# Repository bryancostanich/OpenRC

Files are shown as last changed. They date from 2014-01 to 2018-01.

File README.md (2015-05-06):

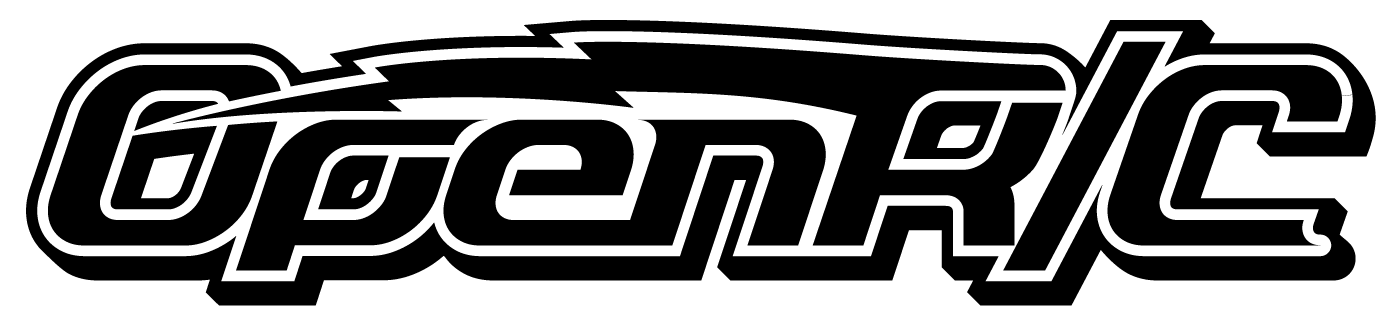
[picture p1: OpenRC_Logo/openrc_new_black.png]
OpenRC Logo


Repo for the OpenRC Printable Radio Controlled Vehicles Project. Contains printable parts, instructions, and parts sourcing info. Based on the [Google Group here](https://plus.google.com/communities/112745535856143176146)

# [General RC Information](RCInfo.md)
Battery info, radio info, etc.

# Projects

## [Truggy](Truggy)

An awesome 4WD 1:10 Scale 3D printable truggy! This pic says all about this sexy beast:

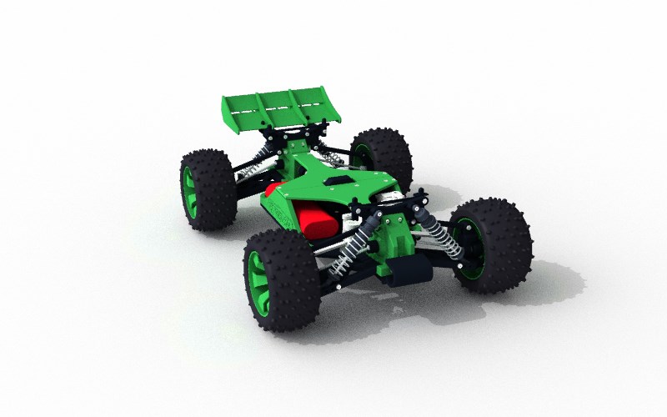
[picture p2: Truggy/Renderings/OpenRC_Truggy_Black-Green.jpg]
Truggy Pic


## [Touring Car](https://github.com/bryancostanich/OpenRC/tree/master/Touring_Car)

4WD 1:10 scale 3D Printable touring car. Also designed by Daniel, the Touring Car was his first attempt at designing an RC Car.

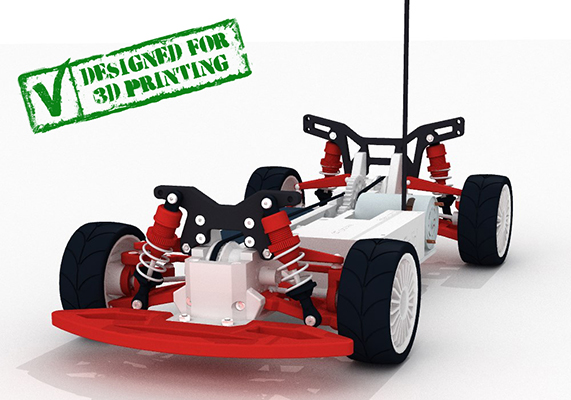
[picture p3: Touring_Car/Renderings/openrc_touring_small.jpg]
Touring Car Pic


## [Ducted Fan Design Library](DuctedFanDesignLibrary)

An electric ducted fan design library written in Python using the Blender API. Currently, the software is in script form, but an add-on of sorts is being created.

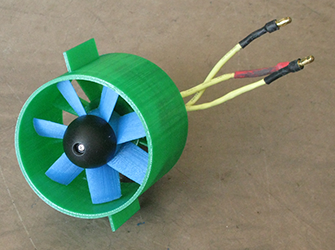
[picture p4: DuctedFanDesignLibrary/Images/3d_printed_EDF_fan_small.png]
Fan


## Authors
 * Truggy - Daniel Norée
 * Ducted Fan Design Library - André Roy

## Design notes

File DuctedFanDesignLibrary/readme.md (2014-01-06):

# Ducted Fan Design Library
An electric ducted fan design library written in Python using the Blender API. Currently, the software is in script form, but an add-on of sorts is being created.

Fan

## Instructions

 * Load blender
 * Split the default 3d window vertically and open the text editor in the new left window.
 * In the text editor open **EDFLibrary.py**, **DLUtils.py**, **TurboMachLib.py** and **GUI.py**
 * Run the **GUI.py** script
 * New tools will appear in the object tools pane of the 3D window on the right.

## License
[GNU Affero GPL V3.0](http://www.gnu.org/licenses/agpl-3.0.html)

Copyright DesignLibre 2013.

Author: André Roy

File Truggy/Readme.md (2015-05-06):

# OpenRC Truggy

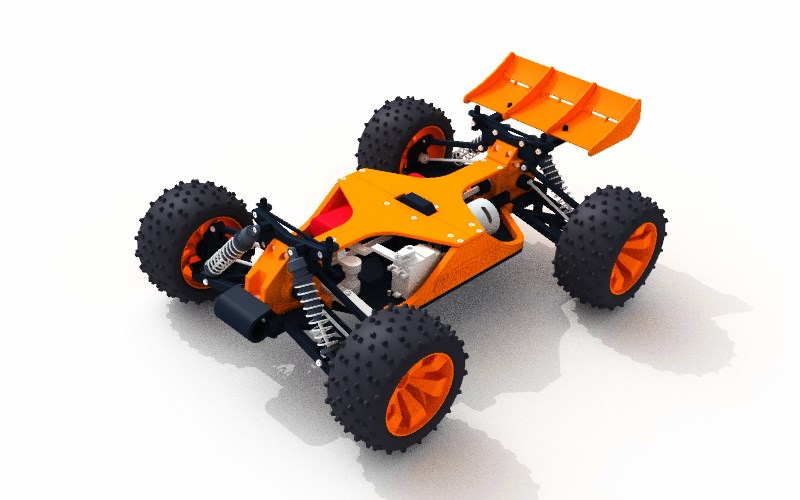
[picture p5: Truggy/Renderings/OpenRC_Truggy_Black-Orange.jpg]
Truggy


## Introduction
 * **video** - [Here](http://www.youtube.com/watch?v=dElz53EsmtM)
 
## License
Truggy has been released under the [Creative Commons 3.0 License](http://creativecommons.org/licenses/by/3.0/), Copyright Daniel Norée
 
## File Organization
I've taken a whack at organizing the files, but please let me know if you want to be added to the repo and organize even more/better.
 
## Bill of Materials and Sourcing Info
 * [here](https://github.com/bryancostanich/OpenRC/blob/master/Truggy/BOM.md)

## Documentation
 * [here](Documentation)

## Specs

### Dimensions
 * **Class** - 1/10 electric 4WD Truggy
 * **Width** - 312 mm
 * **Length** - N/A mm
 * **Wheelbase** - 280 mm
 * **Ready-to-run weight** - 2100 g Chassis

### Chassis Plate
 * **Chassis Plate** - 2Pcs 3D Printed ABS (1 pc version available)
 * **Top Deck** - 2Pcs 3D Printed ABS

### Suspension
 * **Shocks** - 3D Printed Nylon OpenRC Shocks

### Drivetrain
* **Type** - Full-time shaft-drive 4WD
* **Primary** - Pinion / spur
* **Drive shafts** - Reely CVD-cardan shaft (V23581L)
* **Central shafts** - 3DPrintedABSDirectConnectionShafts
* **Differentials** - 3D Printed ABS + Nylon combo
* **Bearings** - Rubber-sealed high-speed bearings

### Gearing
 * **Primary ratio** - ￼1:2.5
 * **Differential pinion** - 16T front / rear
 * **Differential crown gear** - 40T front / rear
 * **Spur gear** - 65T
 * **Motor pinion** - 20T
 
### Geometry
 * **Camber** - Adjustable front & rear, 3D Print replacement parts
 * **Caster** - 6.5º Static
 * **Toe-in** - Adjustable front , 3D Print replacement parts
 * **Steering** - Centrally-positioned dual steering system W/O servo saver
 
### Body, Tires, Wheels & Misc
 * **Body** - HPI Firestorm
 * **Tires** - Losi 320S Zombie Max
 * **Wheels** - 3D Printed ABS OpenRC Truggy Rims
 
### Electronics 
 * **Radio system** - Hobby King GT-2 2.4Ghz 2Ch Tx & Rx
 * **Motor** - Turnigy Trackstar 3650 16T (4000Kv) Brushless Motor
 * **Esc** - Turnigy Trackstar 80A Sensorless Brushless ESC
 * **Battery** - Turnigy 4000mAh 2S 40C Lipo Pack

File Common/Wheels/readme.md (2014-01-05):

# Wheels
 * Beadlock Rim - [outcast RC @ thingiverse](http://www.thingiverse.com/thing:47271)
 * OZ Rally WRC (M-03_OZ-WRC) - [breckandawson @ github](https://github.com/brackendawson/M-03_wheels)
 * my_rim_2.skp - [Cain666 @ Thingiverse.com](http://www.thingiverse.com/thing:144591)]
 * RC Crawler 4x4 - [diegudio @ thingiverse](http://www.thingiverse.com/thing:176945)

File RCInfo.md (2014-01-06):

# RC Vehicle Information
## Battery Choice
 * [LiPo vs. LiFe vs. LiIon Comparison](http://www.brighthubengineering.com/power-generation-distribution/123906-comparison-of-lithium-ion-to-lithium-iron-battery/)

battery comparison

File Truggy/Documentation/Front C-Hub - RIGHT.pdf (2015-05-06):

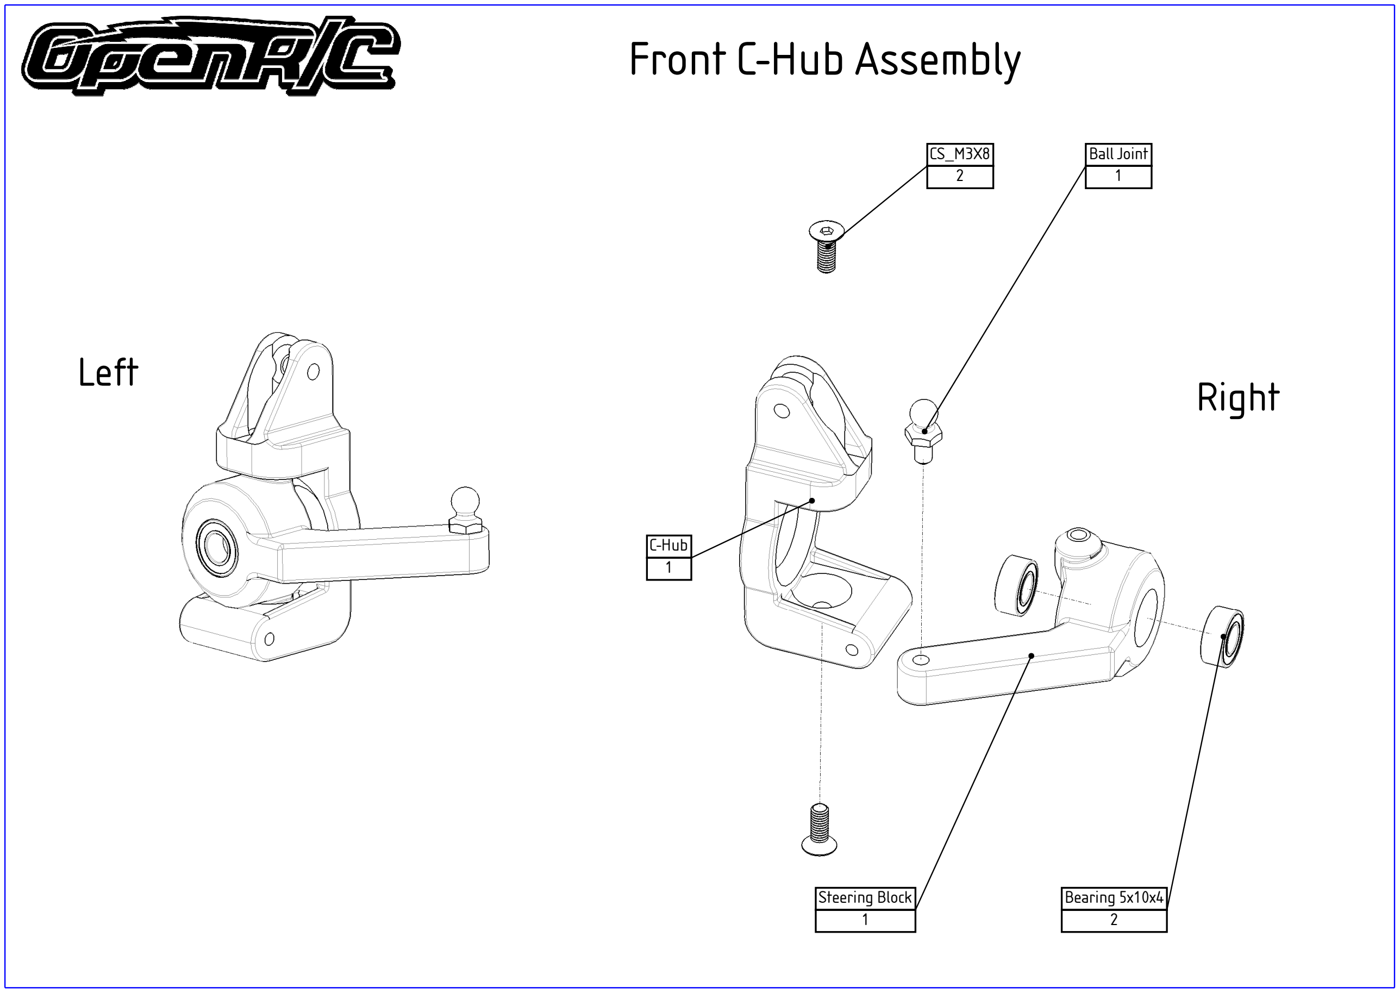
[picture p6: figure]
Front C-Hub Assembly; Left; Right; Bearing 5x10x4 2; C-Hub 1; Steering Block 1; Ball Joint 1

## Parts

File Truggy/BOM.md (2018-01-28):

# Truggy Bill of Materials

## Hardware

### Screws
 * (54) Hexagon Socket Countersunk Head Screw ISO 10642 - M3 × 8 
 * (8) Hexagon Socket Countersunk Head Screw ISO 10642 - M3 × 12
 * (4) Hexagon Socket Countersunk Head Screw ISO 10642 - M3 × 16
 * (10) Hexagon Socket Pan Head Cap Screw ISO 7380 - M3 × 8
 * (10) Hexagon Socket Pan Head Cap Screw ISO 7380 - M3 × 10
 * (12) Hexagon Socket Pan Head Cap Screw ISO 7380 - M3 × 12
 * (4) Hexagon Socket Pan Head Cap Screw ISO 7380 - M3 × 14
 * (4) Hexagon Socket Pan Head Cap Screw ISO 7380 - M3 × 16
 
#### Screw Sources

 * [M3 Hexagon Socket Countersunk Head Screw, various materials and lengths @ Amazon Supply](http://www.amazonsupply.com/s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)
 * [ISO 7380 M3 Button (Pan) Head Cap Screws, various materials and lengths @ Amazon Supply](http://www.amazonsupply.com/s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)
 
###  Nuts

 * (26) M3 Hexagon Nut ISO 4032 - [Amazon Source](http://www.amazon.com/dp/B000FN0CP0/ref=biss_dp_t_asn)
 
### Bearings
 * (10) 10x15x4 - [Amazon Supply Source](http://www.amazonsupply.com/s/ref=sp_search?guess=true&Action=submit&keywords=10x15x4+bearing)
 * (8) 5x10x4 - [Amazon Supply Source](http://www.amazonsupply.com/s/ref=sp_search?guess=true&Action=submit&keywords=5x10x4+bearing)
 * (4) 6x12x4 - [Amazon Supply Source](http://www.amazonsupply.com/s/ref=sp_search?guess=true&Action=submit&keywords=6x12x4+bearing)

### Rods
 * (4) Ø2.0 x 32mm
 * (3) Ø3.0 x 18mm
 * (4) Ø3.0 x 56mm
 * Optional: Ø2.0 x 10mm for internal driveshafts
 
### Drivetrain
 * (4) Outer Driveshafts - CVD 1:10 118MM (See sources)
 
### Wheels
 * (4) Rims - Printed OpenRC
 * (4) Tires - Losi 320S Zombie Max Tire with Foam LOSB7213
 
### Suspension
 * (4) 100mm Standard RC Car Shocks
 	* [Blue Aluminum @ HobbyKing.com](http://www.hobbyking.com/hobbyking/store/__22499___1_10_Model_Car_100mm_Adjustable_Aluminum_Shock_Absorber_2pc_Blue_.html)
 	* [Purple Aluminum @ HobbyKing.com](http://www.hobbyking.com/hobbyking/store/__26276__1_10_Car_100mm_Aluminum_Shock_Absorber_Purple_2pcs_bag_.html)
 	* [Silver Aluminum @ HobbyKing](http://www.hobbyking.com/hobbyking/store/__22500__1_10_Model_Car_100mm_Adjustable_Aluminum_Shock_Absorber_2pc_.html)
 	* [Gun Metal Aluminum with Three Pairs of Various Strength Spings @ TowerHobby.com](http://www3.towerhobbies.com/cgi-bin/wti0001p?&I=LXDCTM&P=7)
 
###  Body
 * Body - HPI Firestorm DSX-1 Lexan Truck Body HPI7123
 
## RC Components

### Motor + Electronic Speed Controller (ESC)
Standard 1:10  motor rated for 4WD.

 * [Castle Creations SV3 Sidewinder 6900kV @ TowerHobbies.com](http://www3.towerhobbies.com/cgi-bin/wti0001p?&I=LXDAVR&P=7)
 * [Castle Creations SV3 Sidewidner 7700kV @ TowerHobbies.com](http://www3.towerhobbies.com/cgi-bin/wti0001p?&I=LXDAVS&P=7)
 * [OUT OF STOCK - Turnigy TrackStar Waterproof 1/10 Brushless Power System 4000KV/80A (Motor+ESC Combo)](http://www.hobbyking.com/hobbyking/store/uh_viewItem.asp?idProduct=25138 @ HobbyKing.com)

### Battery

 * [Turnigy 4000mAh 2S 40C Lipo Pack @ HobbyKing.com](http://www.hobbyking.com/hobbyking/store/RC_PRODUCT_SEARCH.asp?strSearch=Turnigy+4000mAh+2S+40C)

### Battery Charger

 * [Ace T6DC Digital Multi Charger @ TowerHobbies.com](http://www3.towerhobbies.com/cgi-bin/wti0001p?&I=LXBFDR&P=7)

### Servo

 * [BMS-620MG High Torque Servo (Metal Gear) 9.1kg / .15sec / 50g](http://www.hobbyking.com/hobbyking/store/RC_PRODUCT_SEARCH.asp?strSearch=BMS-620MG)

### Radio

Standard 2 Channel Transmitter and Receiver (Radio System)

 * [Hobby King GT-2 2.4Ghz 2Ch Radio System](http://www.hobbyking.com/hobbyking/store/RC_PRODUCT_SEARCH.asp?strSearch=Hobby+King+GT-2+2.4Ghz+2Ch)
 * [Tower Hobbies 224 2-channel 2.4ghz Radio System](http://www3.towerhobbies.com/cgi-bin/wti0001p?&I=LXWPW0&P=7)
 * [Tactic TTX240 2-Channel SLT 2.4ghz Radio System @ TowerHobbies.com](http://www3.towerhobbies.com/cgi-bin/wti0001p?&I=LXWRP3&P=7)
 * [HPI Racing TF-40 2.4ghz Radio System @ TowerHobbies.com](http://www3.towerhobbies.com/cgi-bin/wti0001p?&I=LXCEHR&P=7)
 * [Axial AX-3 2-Channel 2.4ghz Radio System @ TowerHobbies.com](http://www3.towerhobbies.com/cgi-bin/wti0001p?&I=LXBMCM&P=7)
 
### CVD Shafts
 * [Conrad](http://www.conrad.com/ce/en/product/231121/)

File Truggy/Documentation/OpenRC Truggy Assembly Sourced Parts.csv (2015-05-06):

Name |  |  |  |  |  | Quantity
Adhesive tape (For battery holder) | 1
Ball Joint |  |  |  |  | 5
Bearing 5x10x4 |  |  |  | 8
Bearing 6x12x4 |  |  |  | 4
Bearing 10x15x4 |  |  |  | 10
CS_M3X5,5 (Cut from a longer screw) | 1
CS_M3X8 |  |  |  |  | 54
CS_M3X10 |  |  |  |  | 6
CS_M3x14 |  |  |  |  | 4
CS_M3x16 |  |  |  |  | 6
HSC_M3X8 |  |  |  |  | 3
HSC_M3X10 |  |  |  |  | 14
HSC_M3X14 |  |  |  |  | 8
HSC_M3X16 |  |  |  |  | 14
NUT_M3 |  |  |  |  | 26
NUT_M4 |  |  |  |  | 4
Pin 2x10 |  |  |  |  | 8
Pin 2x32 |  |  |  |  | 4
Pin 3x18 |  |  |  |  | 3
Pin 3x56 |  |  |  |  | 4
CVD Driveshaft 118mm |  |  | 4
Velcro (For battery holder) |  | 1

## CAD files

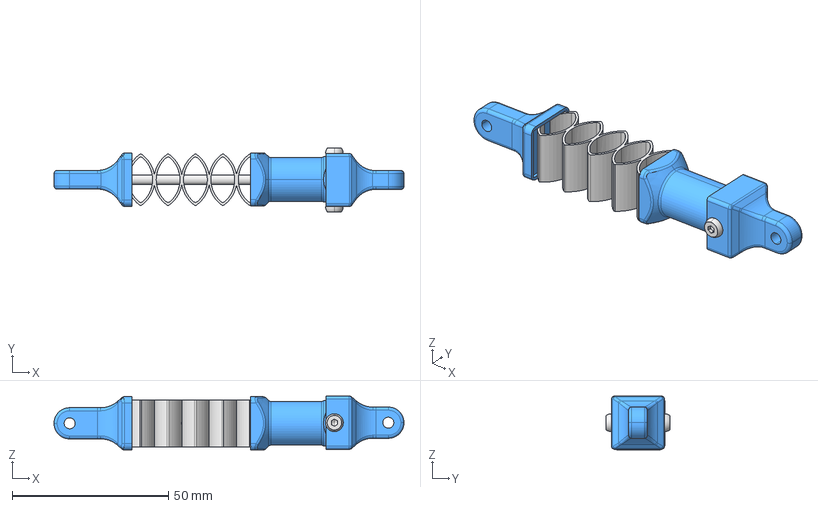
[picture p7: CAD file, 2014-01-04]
Truggy/STLs of Components for Printing/Suspension/Experimental Shocks/STP/Open RC Experimental Shock Assembly.stp
111.9 x 20.3 x 17.2 mm
Spring
Bottom
Lid
Hexagon Socket Head Cap Screw ISO 4762 - M3 _ 30
Hexagon Socket Pan Head Cap Screw ISO 7380 - M3 × 6 x 2

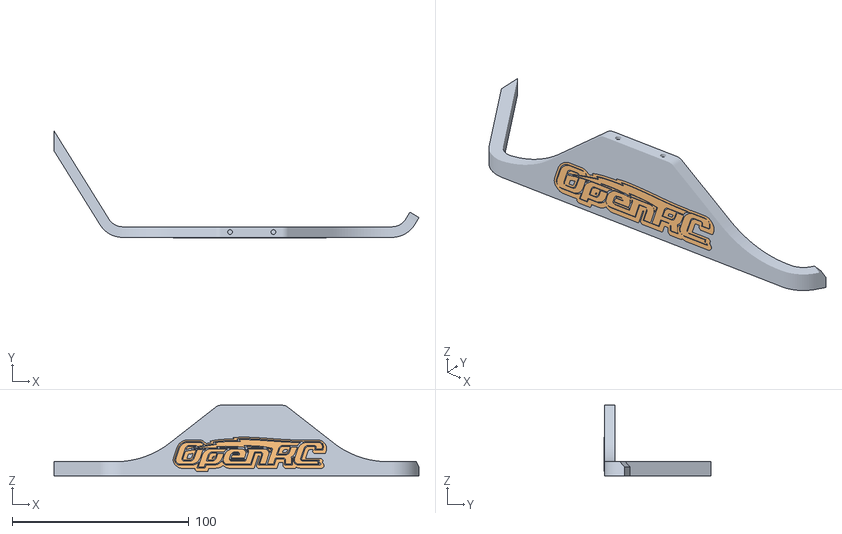
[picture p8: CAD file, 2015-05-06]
Truggy/STLs of Components for Printing/Chassis/Right Shield Assy w Logo.stl
206.8 x 60.8 x 40.0

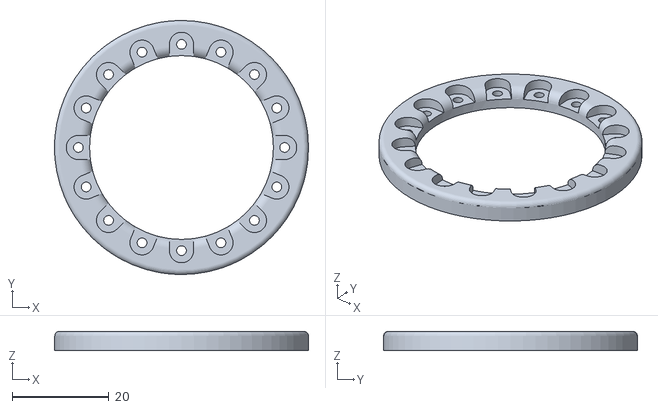
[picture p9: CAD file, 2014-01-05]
Common/Wheels/Beadlock Rim/bead_thick.stl
52.5 x 52.5 x 4.00

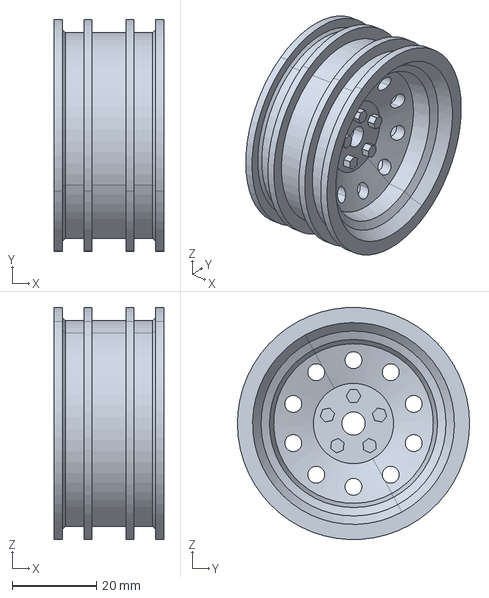
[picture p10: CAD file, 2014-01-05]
Common/Wheels/RC Crawler 4x4 Rim/llanta_v1.1.stp
26.0 x 55.0 x 55.0 mm

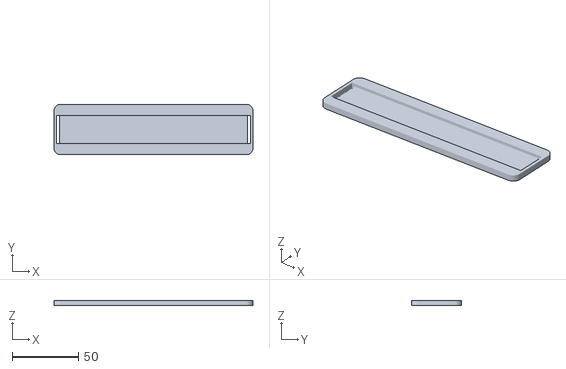
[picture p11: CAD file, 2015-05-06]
Truggy/STLs of Components for Printing/Battery Holder/Battery Holder.stl
150.0 x 38.0 x 4.00

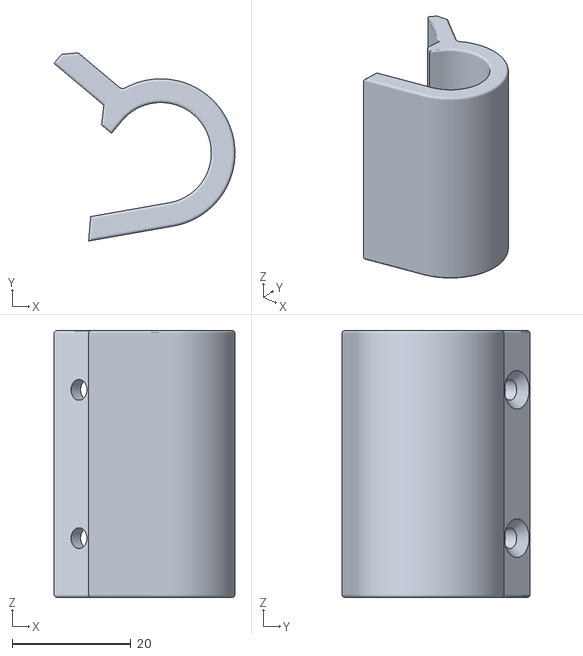
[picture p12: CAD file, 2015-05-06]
Truggy/STLs of Components for Printing/Bumper/Bumper.stl
30.5 x 31.7 x 45.0

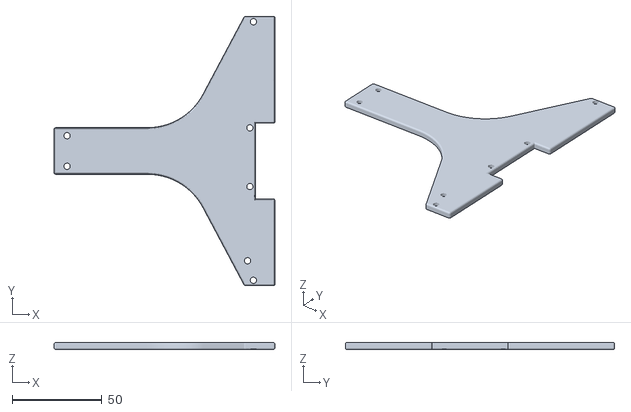
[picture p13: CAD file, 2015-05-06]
Truggy/STLs of Components for Printing/Chassis/Top Deck Rear.stl
123.1 x 150.0 x 4.00

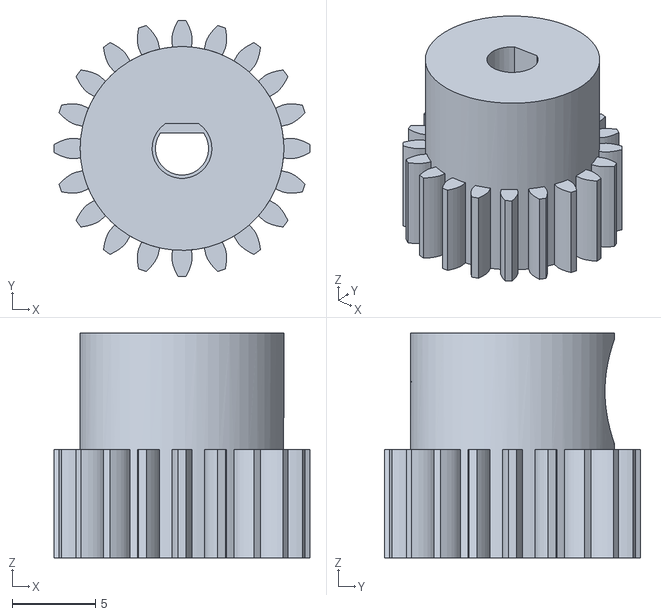
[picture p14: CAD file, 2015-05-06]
Truggy/STLs of Components for Printing/Drive Train/Spur Gear 20T.stl
15.4 x 15.4 x 13.5

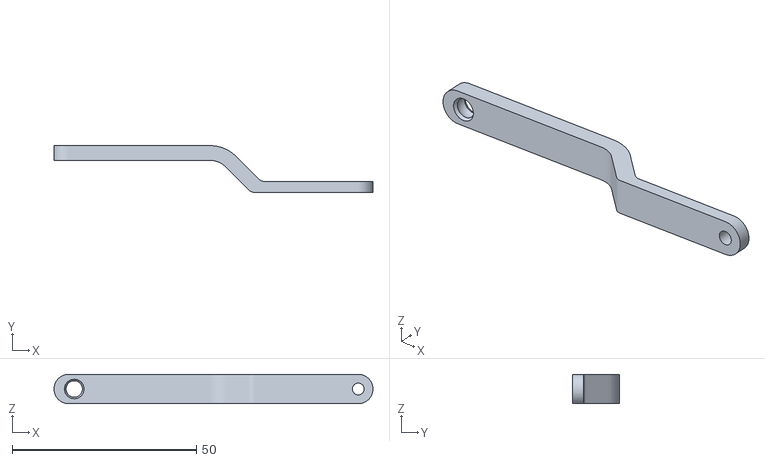
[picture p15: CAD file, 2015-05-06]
Truggy/STLs of Components for Printing/Electronics Holders/Servo Arm.stl
86.6 x 12.7 x 8.00

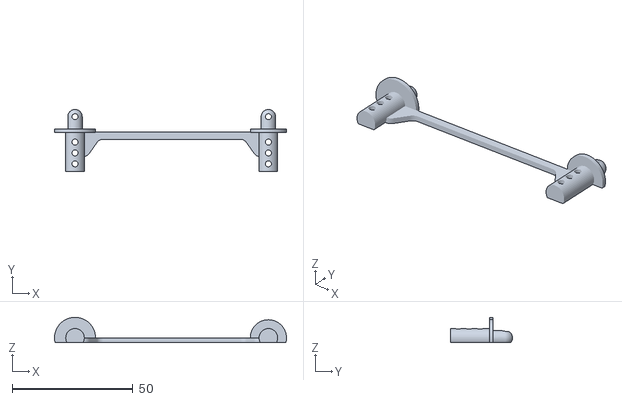
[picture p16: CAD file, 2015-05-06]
Truggy/STLs of Components for Printing/Misc/Simple Body Holder.stl
96.0 x 25.7 x 10.5

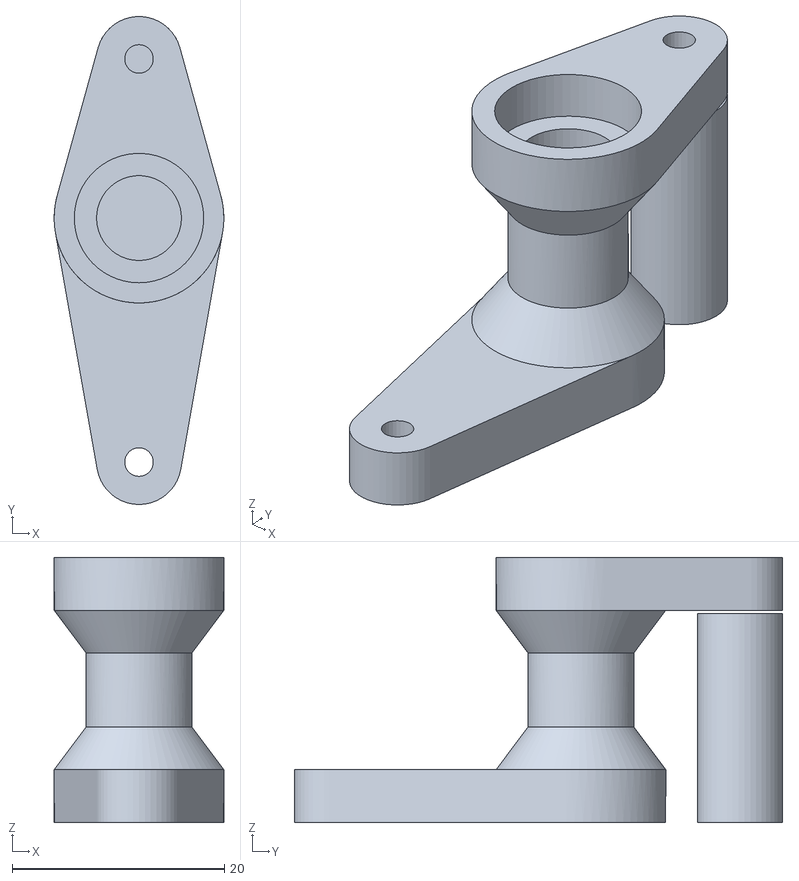
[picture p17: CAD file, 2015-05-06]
Truggy/STLs of Components for Printing/Steering/Steering Part 2.stl
16.0 x 46.0 x 25.0

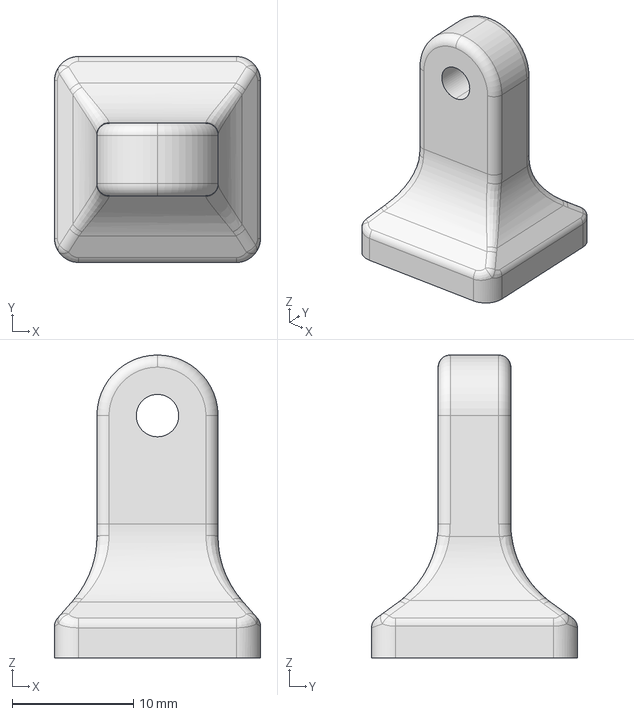
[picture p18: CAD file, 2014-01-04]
Truggy/STLs of Components for Printing/Suspension/Experimental Shocks/STP/Bottom.stp
17.0 x 17.0 x 25.0 mm

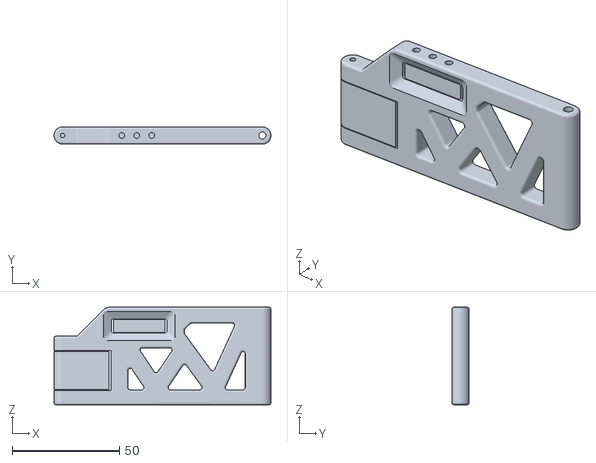
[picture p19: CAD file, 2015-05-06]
Truggy/STLs of Components for Printing/Suspension/Wishbone Front For 118mm Driveshaft.stl
101.0 x 8.00 x 45.5

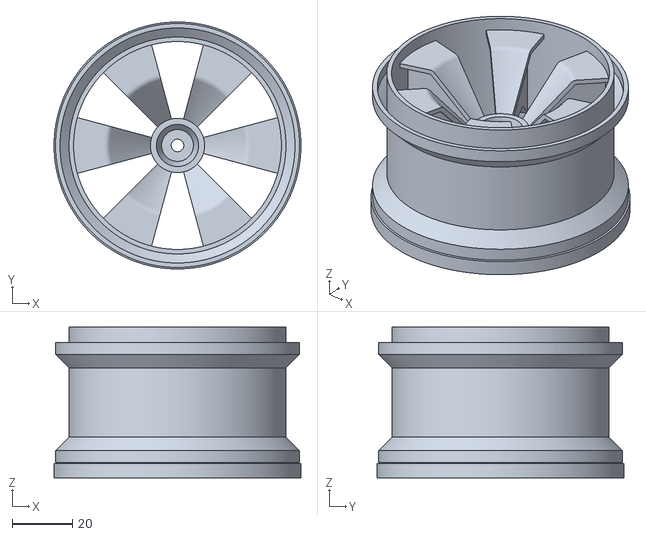
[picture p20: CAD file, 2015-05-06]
Truggy/STLs of Components for Printing/Wheels + Tires/OpenRC Truggy Rim.stl
82.0 x 82.0 x 50.0

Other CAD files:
Truggy/STLs of Components for Printing/Chassis/Left Shield Assy w Logo.stl
Common/Wheels/OZ Rally WRC/M-03_OZ-WRC.stl
OpenRC_Logo/openrc_new_dxf.dxf
Truggy/Tools/STP/Diff Tool.stp
Common/Wheels/Beadlock Rim/bead-scalllop.stl
Common/Wheels/Beadlock Rim/bead-toothed.stl
Common/Wheels/Beadlock Rim/bead-wide.stl
Common/Wheels/Beadlock Rim/bead.stl
Common/Wheels/Beadlock Rim/rim-5spoke.stl
Common/Wheels/Beadlock Rim/rim-8spoke.stl
Common/Wheels/Beadlock Rim/rim-largeholes.stl
Common/Wheels/Beadlock Rim/rim-slot.stl
Common/Wheels/Beadlock Rim/rim-smallholes.stl
Common/Wheels/Beadlock Rim/ring.stl
Common/Wheels/RC Crawler 4x4 Rim/llanta_v1.1.CATPart
Common/Wheels/RC Crawler 4x4 Rim/llanta_v1.1.igs
Common/Wheels/RC Crawler 4x4 Rim/llanta_v1.1.stl
Common/Wheels/my_rim_2.skp
Truggy/STLs of Components for Printing/Chassis/Chassie Plate Front.stl
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

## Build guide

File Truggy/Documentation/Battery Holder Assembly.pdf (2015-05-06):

# Battery Holder Assembly

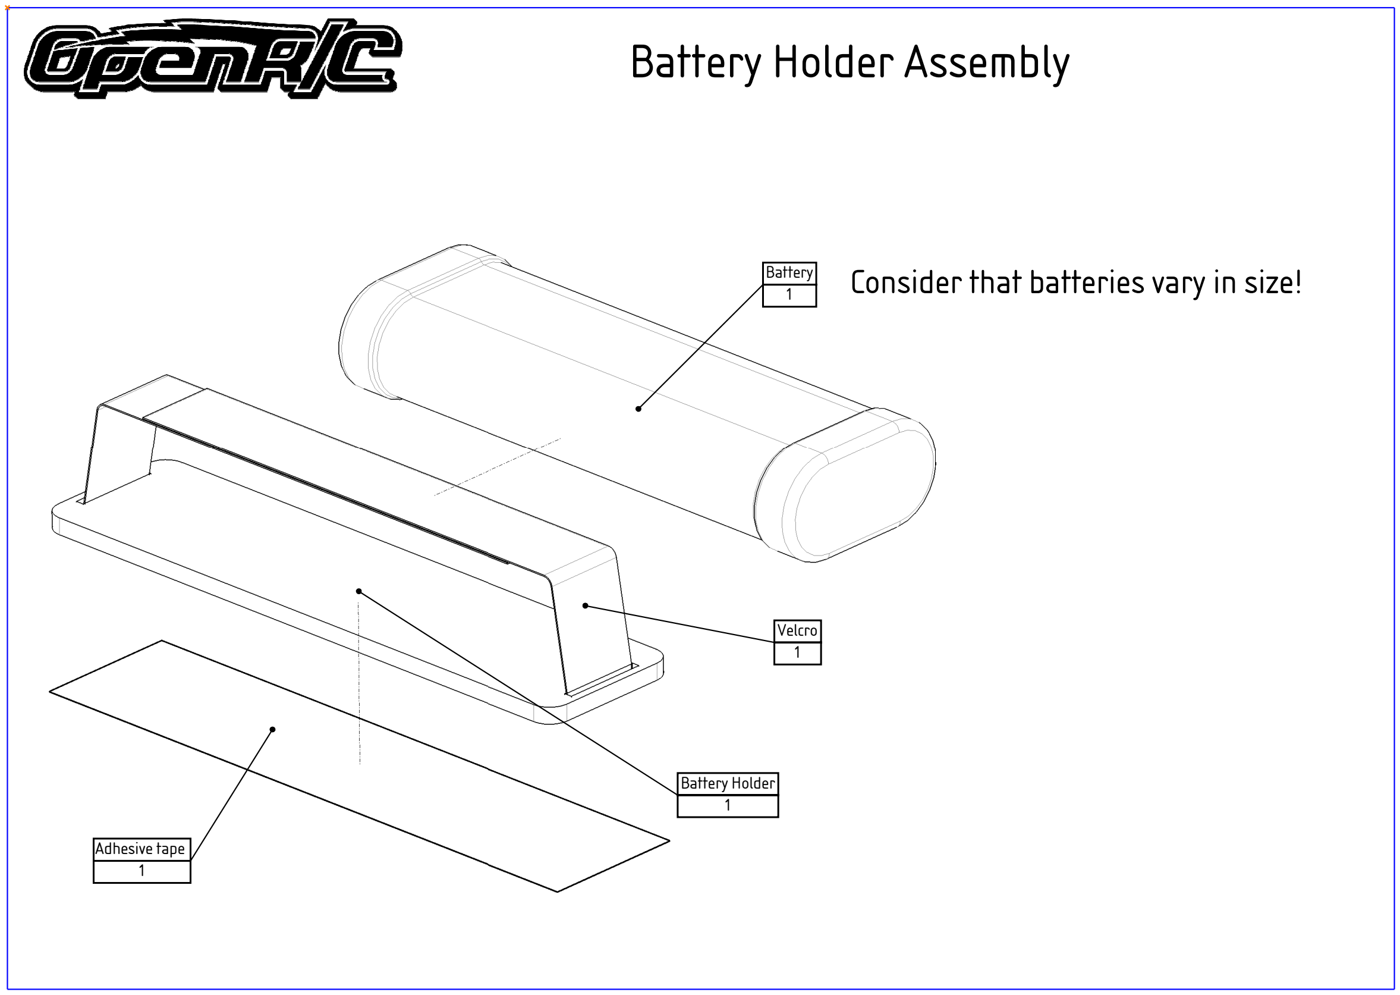
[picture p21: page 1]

Velcro
1

Battery
1

Adhesive tape
1

Battery Holder
1

# Consider that batteries vary in size!

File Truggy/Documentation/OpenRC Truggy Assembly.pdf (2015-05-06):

OpenRC Truggy Assembly

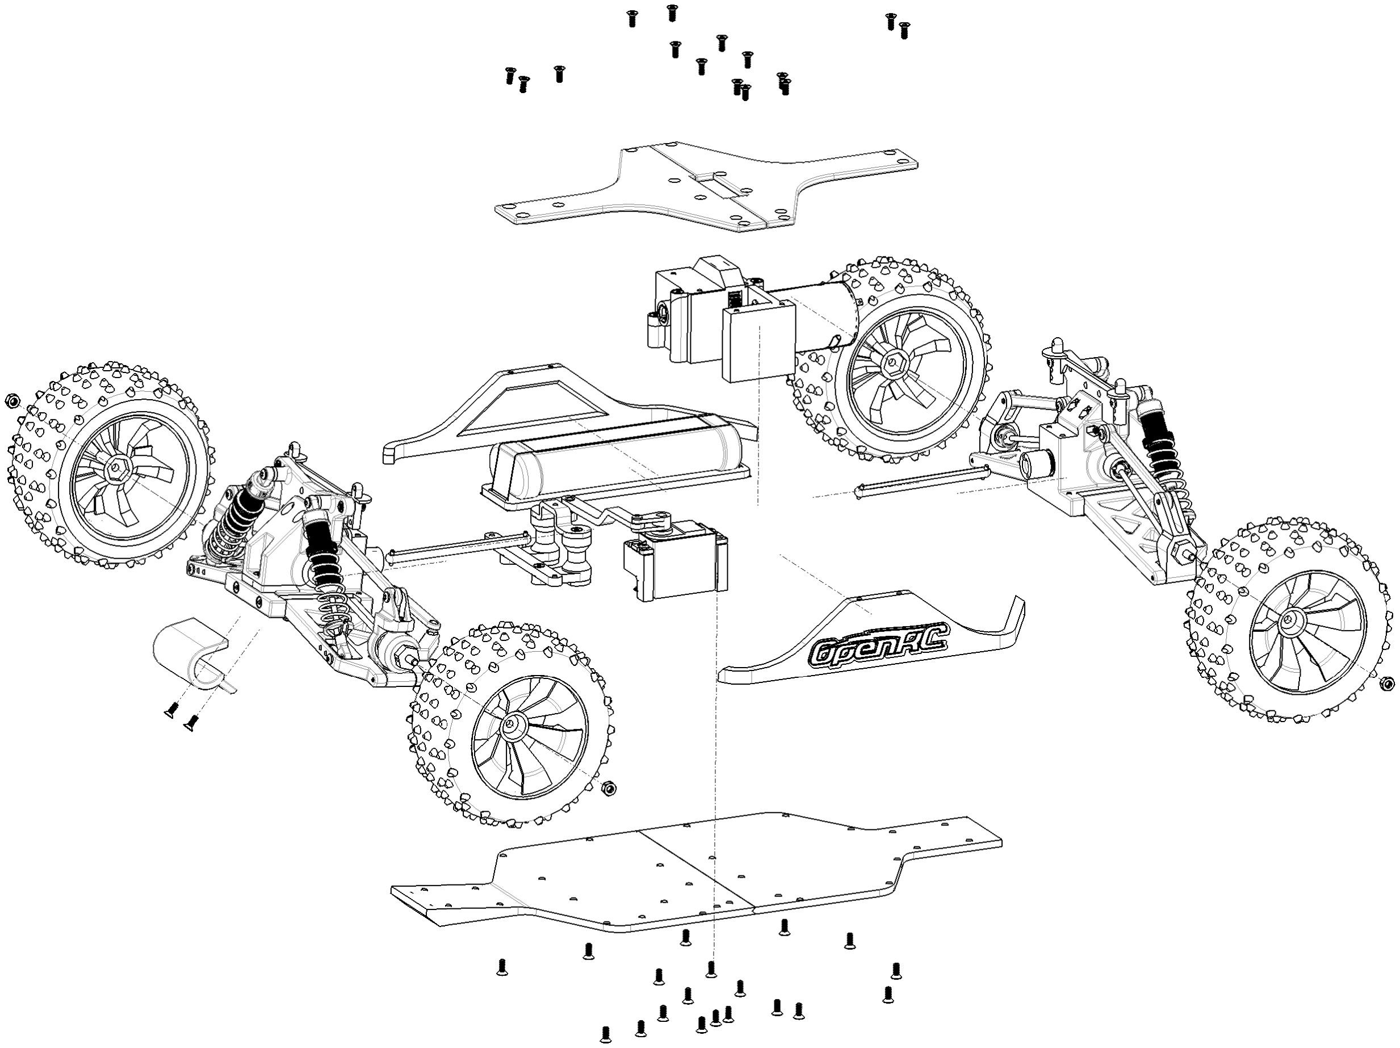
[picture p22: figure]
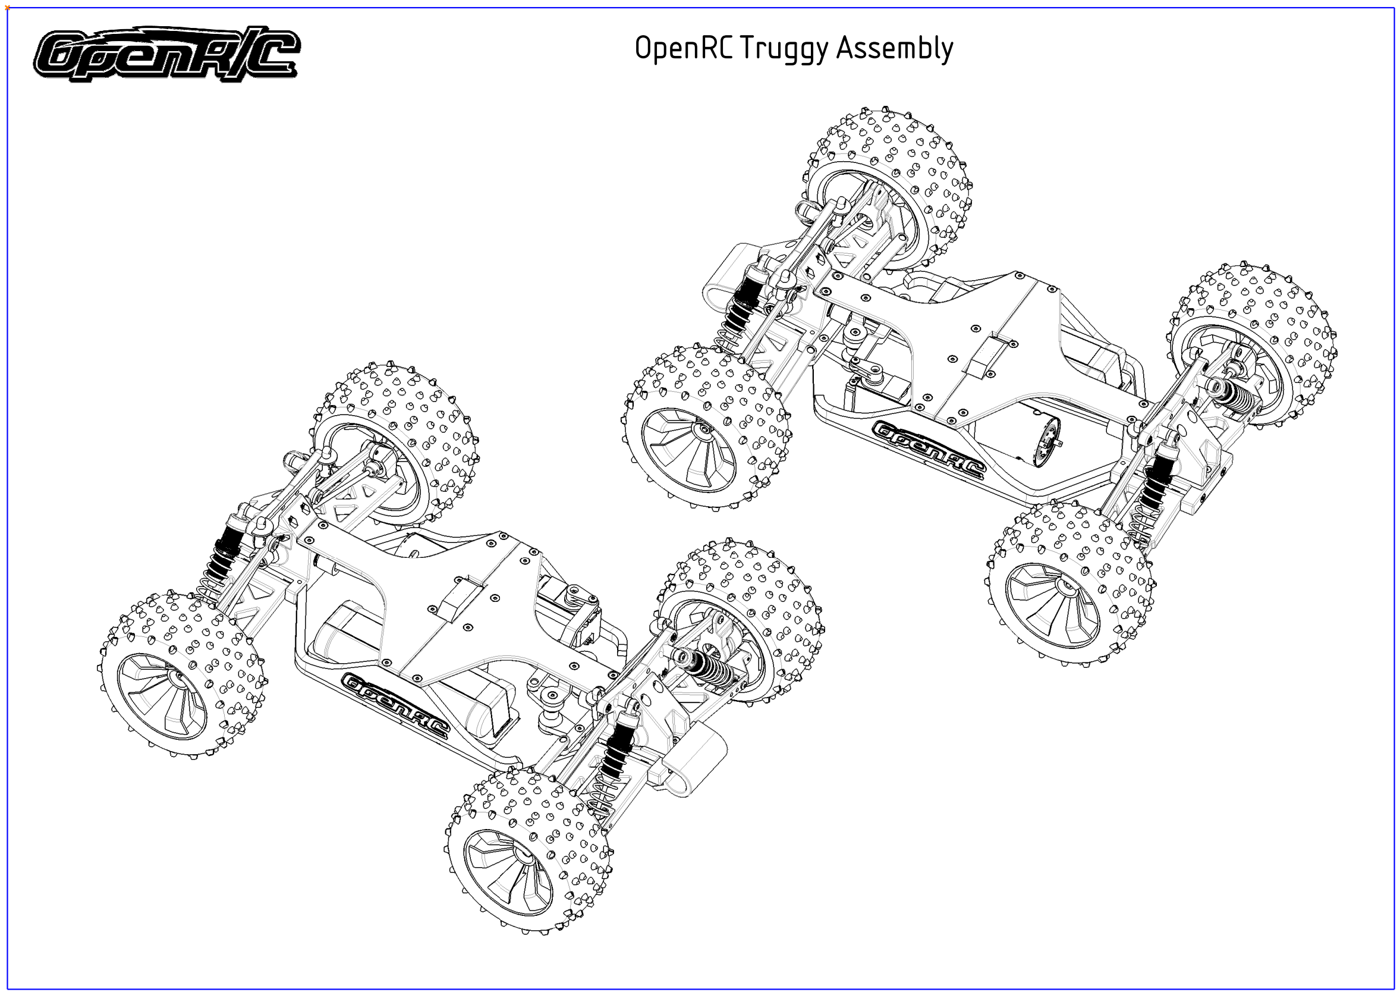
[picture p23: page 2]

OpenRC Truggy Assembly

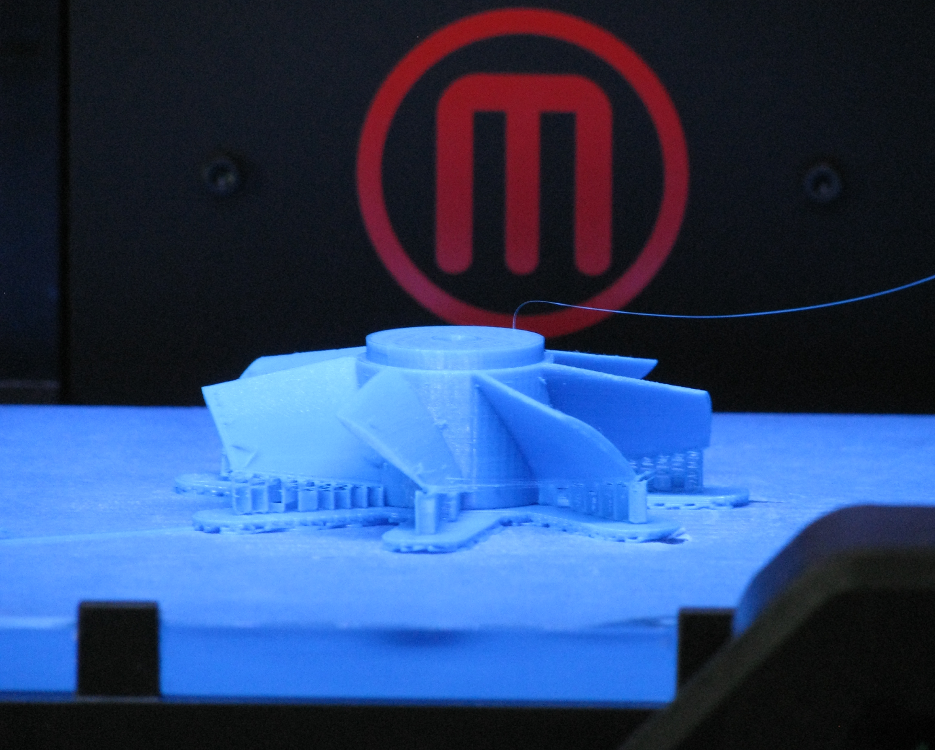
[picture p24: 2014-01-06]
DuctedFanDesignLibrary/Images/blue_3d_printed_EDF_rotor.png

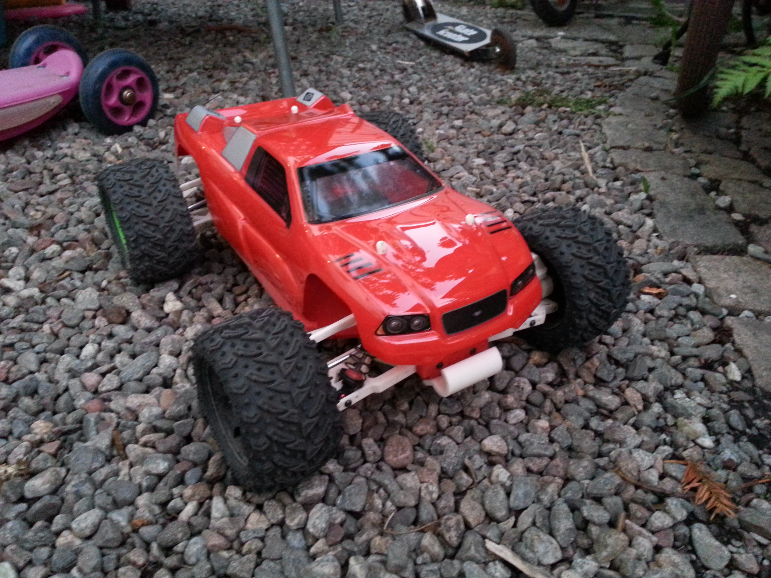
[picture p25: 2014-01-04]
Truggy/Build Pictures/IMG_20130603_220738.jpg

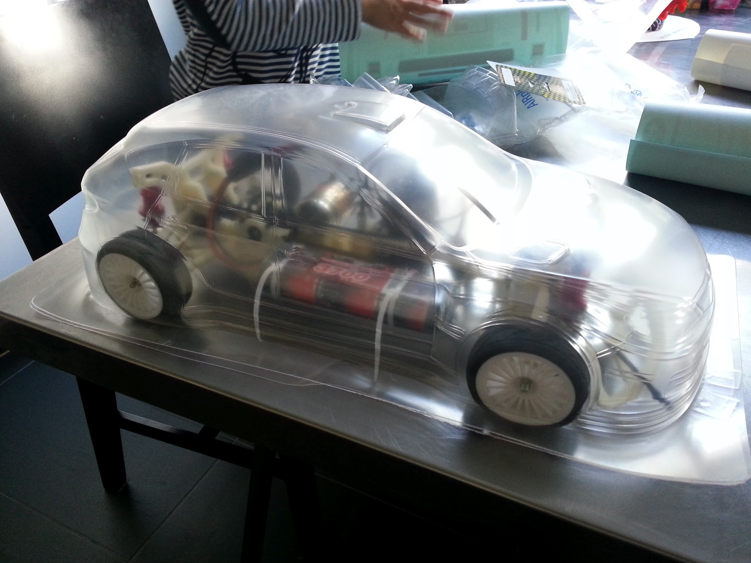
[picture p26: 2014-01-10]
Touring_Car/Build Pictures/20120813_150916.jpg

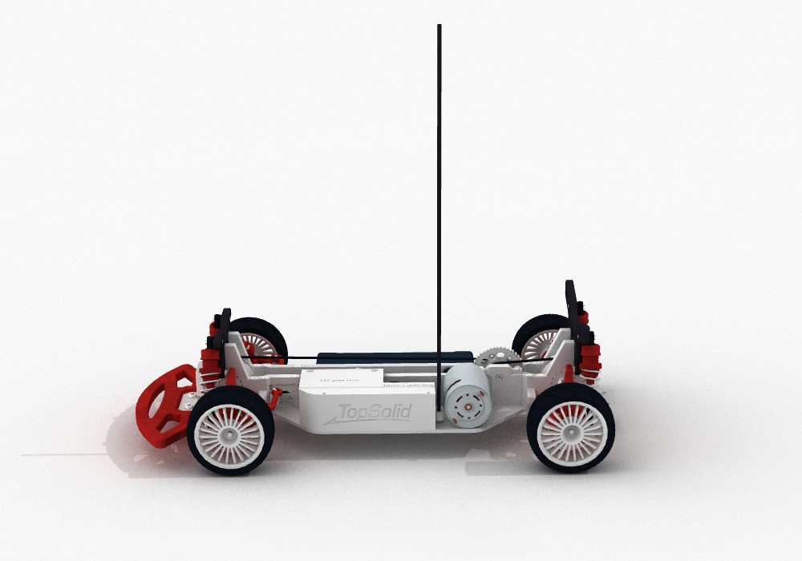
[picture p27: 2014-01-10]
Touring_Car/Renderings/Car Assembly side.jpg

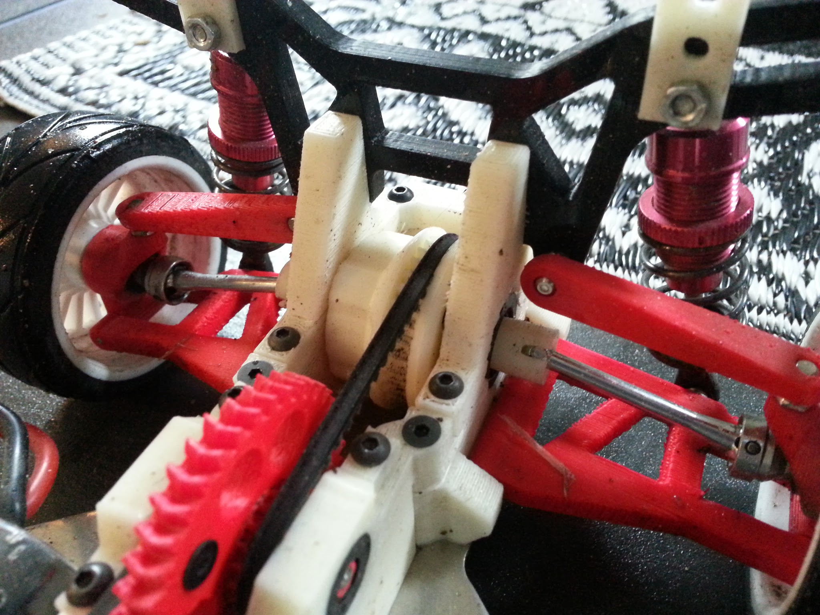
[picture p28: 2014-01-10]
Touring_Car/Build Pictures/IMG_20121110_103743.jpg

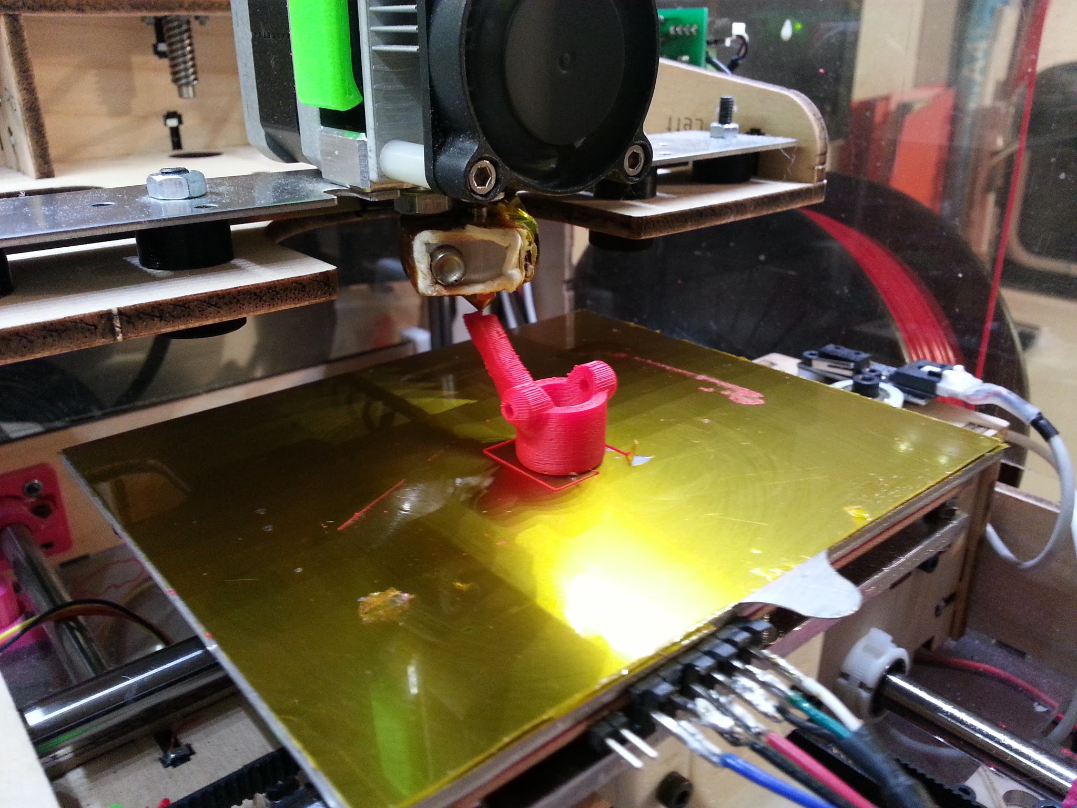
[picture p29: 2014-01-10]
Touring_Car/Build Pictures/20120925_214647.jpg

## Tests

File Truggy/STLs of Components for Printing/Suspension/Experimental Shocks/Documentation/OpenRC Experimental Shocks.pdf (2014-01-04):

### OpenRC Experimental Shocks

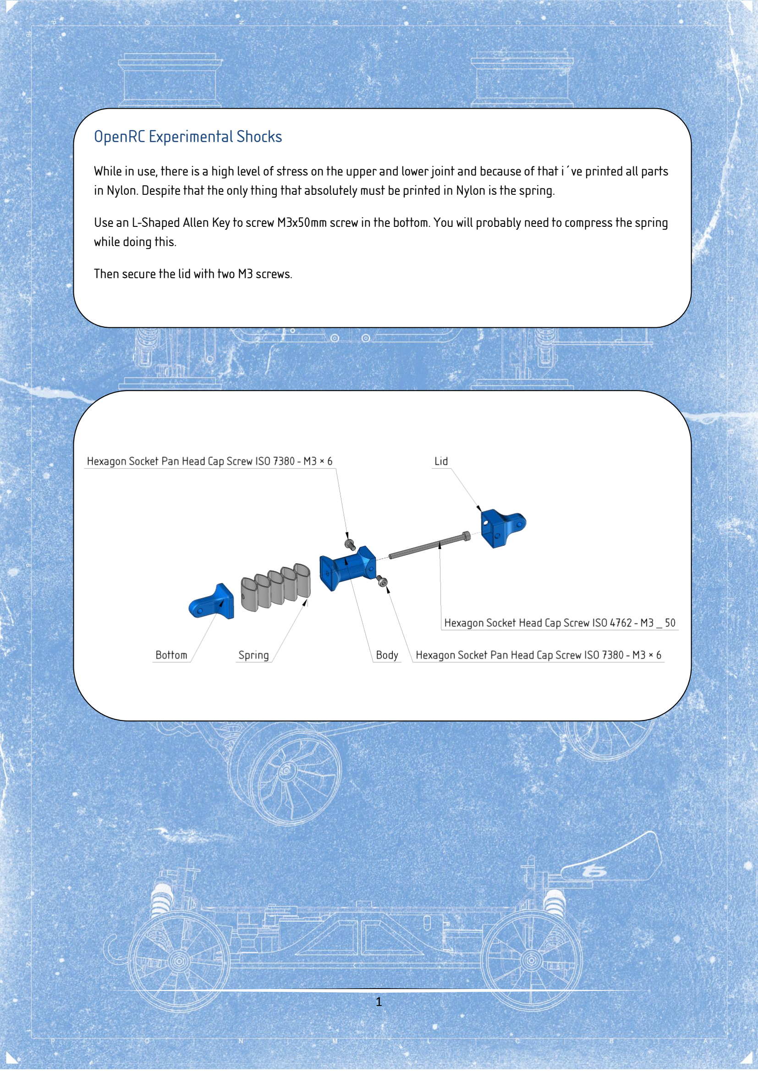
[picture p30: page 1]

1

While in use, there is a high level of stress on the upper and lower joint and because of that i´ve printed all parts in Nylon. Despite that the only thing that absolutely must be printed in Nylon is the spring.

Use an L-Shaped Allen Key to screw M3x50mm screw in the bottom. You will probably need to compress the spring while doing this.

Then secure the lid with two M3 screws.

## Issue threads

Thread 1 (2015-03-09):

Ball connectors

cheeseoverdose, 2015-03-09:
this doesn't include the ball connectors for this build

eLEcTRiCZiTy, 2019-05-03:
Please, include Ball Joints, etc. into BOM.

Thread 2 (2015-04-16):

Bearing 3x10x4 should be 5x10x4?

jb137, 2015-04-16:
Bearings arrived today. But the 3x10x4 does not fit in the CVDs from Conrad. I just discovered the openrcproject BOM page shows 5x10x4 bearings. Please correct the BOM to prevent others from ordering the wrong diameter.

Closed 2018-01-28.

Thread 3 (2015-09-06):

Amazon Supply in Truggy/BOM.md no longer exists

kcleung, 2015-09-06:
When I went through your BOM for the Truggy, all links to "Amazon Supply" or "Amazon Supply Source" are dead, as Amazon Supply has already been rebranded as "Amazon Business"  Could you please update the links?

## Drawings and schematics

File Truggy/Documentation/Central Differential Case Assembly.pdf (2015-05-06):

# Central Differential Case Assembly

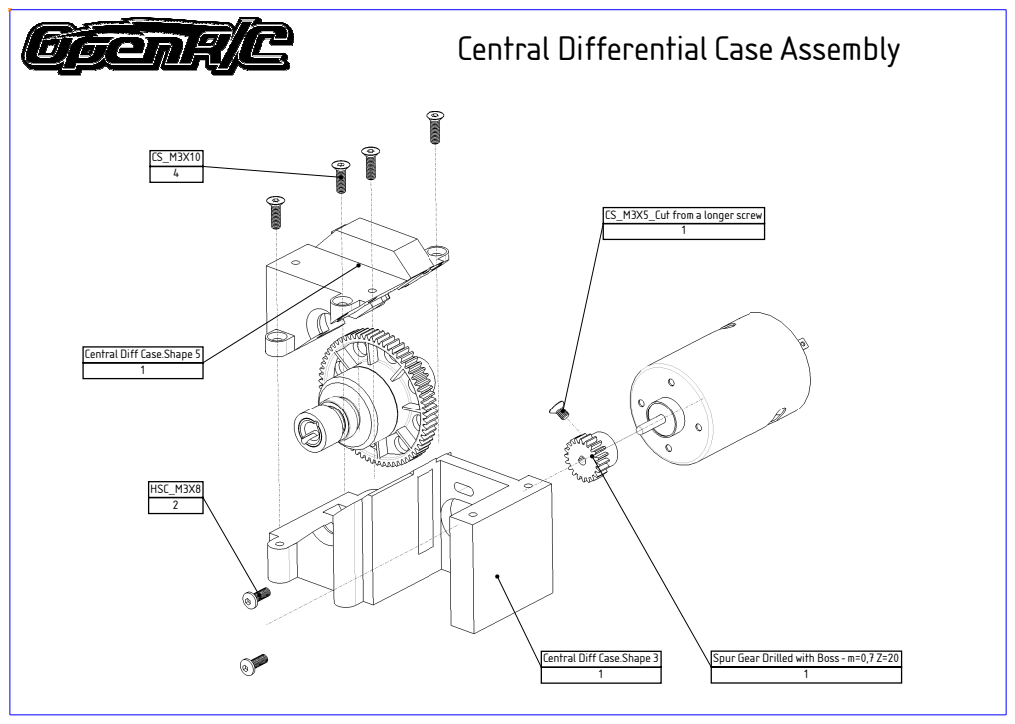
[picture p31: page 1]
HSC_M3X8 2

CS_M3X5_Cut from a longer screw

Central Diff Case.Shape 5

Central Diff Case.Shape 3

Spur Gear Drilled with Boss - m=0,7 Z=20

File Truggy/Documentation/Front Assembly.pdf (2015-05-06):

# Front Assembly

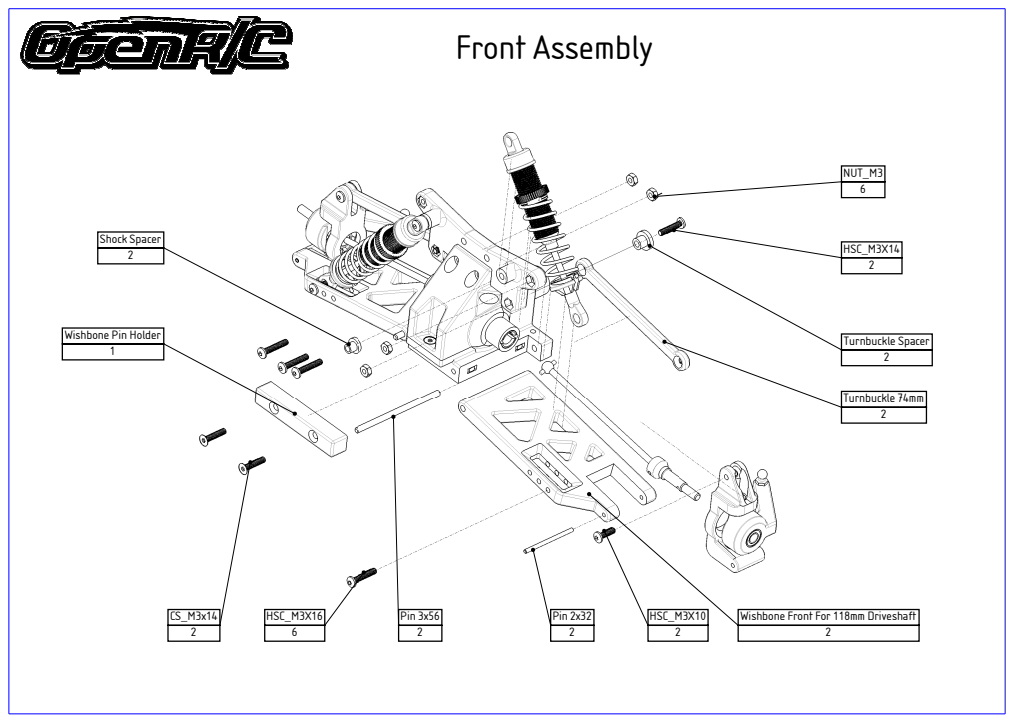
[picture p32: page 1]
HSC_M3X16 6; HSC_M3X14 2; Turnbuckle Spacer 2; Turnbuckle 74mm 2; HSC_M3X10 2; NUT_M3 6; Shock Spacer 2; Pin 3x56 2; Pin 2x32 2

Wishbone Pin Holder

Wishbone Front For 118mm Driveshaft

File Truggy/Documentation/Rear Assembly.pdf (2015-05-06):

# Rear Assembly

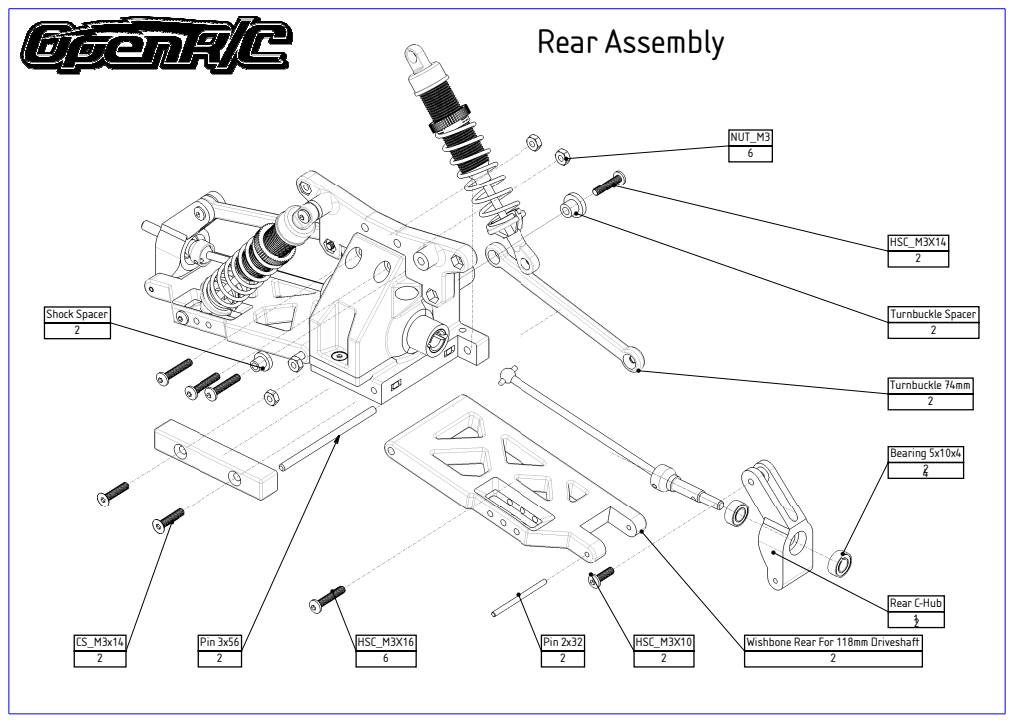
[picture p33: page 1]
Bearing 5x10x4 2; Rear C-Hub 1; Pin 3x56 2; HSC_M3X16 6; HSC_M3X14 2; NUT_M3 6; Turnbuckle Spacer 2; Turnbuckle 74mm 2; HSC_M3X10 2; Shock Spacer 2; Pin 2x32 2

Wishbone Rear For 118mm Driveshaft

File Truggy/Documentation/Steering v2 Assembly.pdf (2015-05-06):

# Steering Assembly

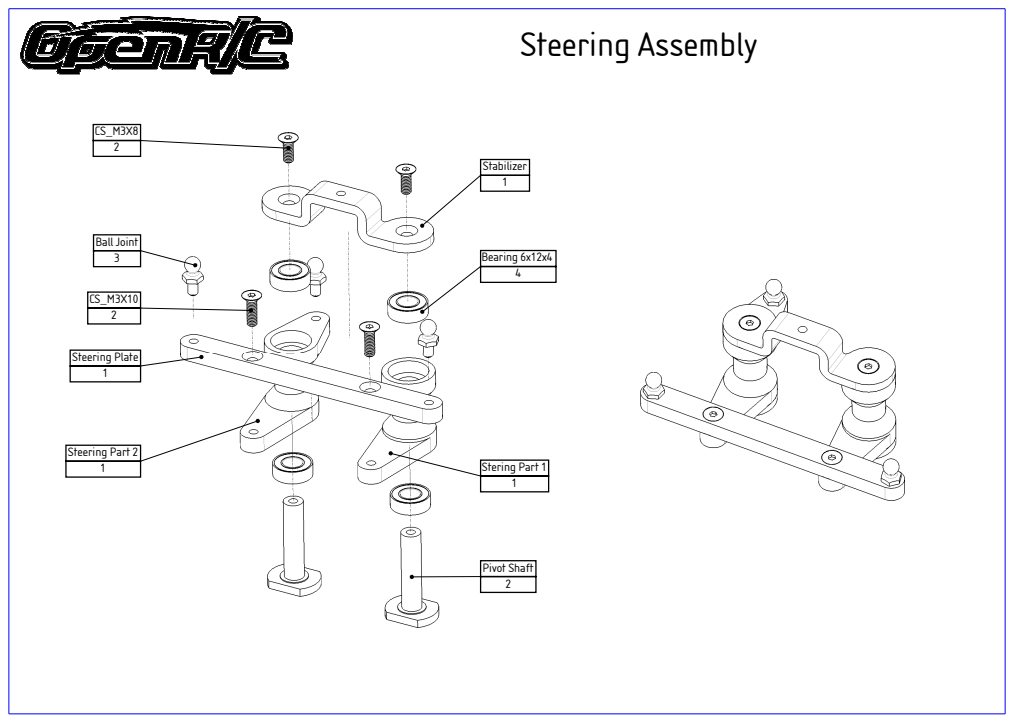
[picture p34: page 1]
Bearing 6x12x4 4; Ball Joint 3; Steering Plate 1; Steering Part 2 1; Stabilizer 1; Stering Part 1 1; Pivot Shaft 2

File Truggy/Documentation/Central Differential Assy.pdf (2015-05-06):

# Central Differential Assembly

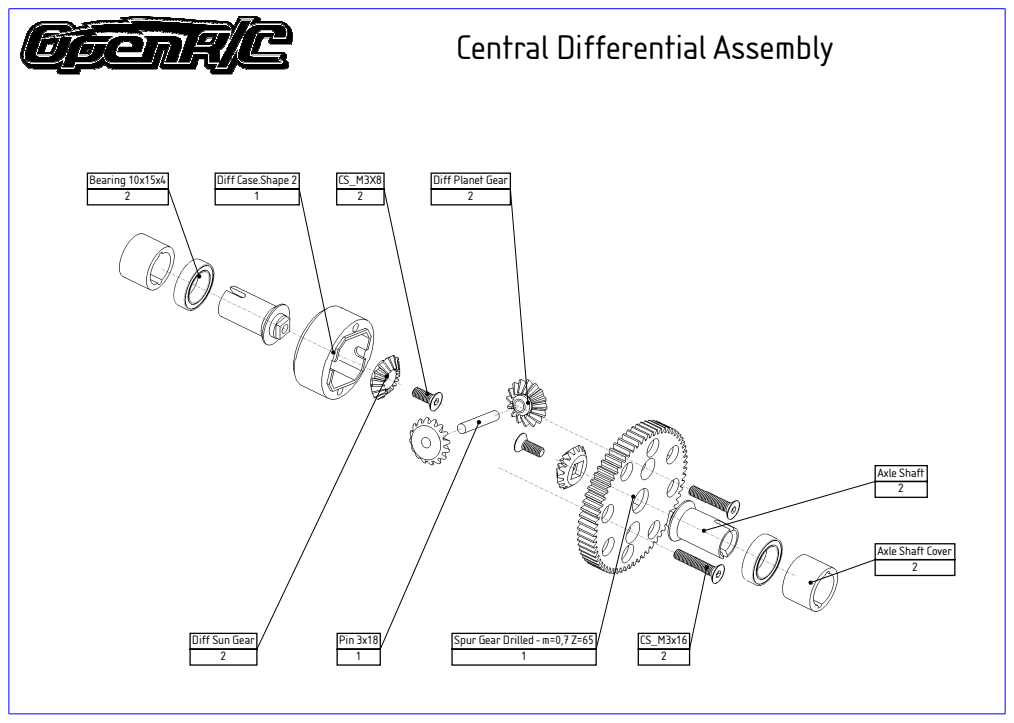
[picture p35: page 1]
Axle Shaft 2; Bearing 10x15x4 2; Pin 3x18 1

Diff Case.Shape 2

Diff Planet Gear

Axle Shaft Cover

Diff Sun Gear

Spur Gear Drilled - m=0,7 Z=65

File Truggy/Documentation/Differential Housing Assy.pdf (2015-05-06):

# Differential Housing Assembly

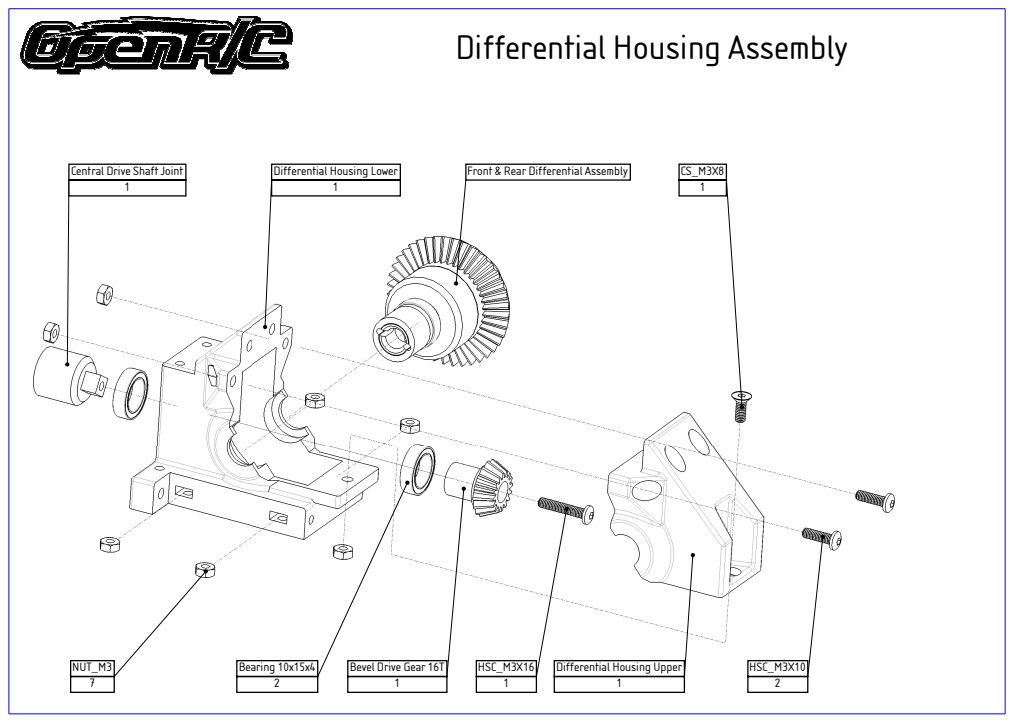
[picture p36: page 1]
HSC_M3X10 2; HSC_M3X16 1; NUT_M3 7; Bearing 10x15x4 2

Central Drive Shaft Joint

Differential Housing Lower

Front & Rear Differential Assembly

Bevel Drive Gear 16T

Differential Housing Upper

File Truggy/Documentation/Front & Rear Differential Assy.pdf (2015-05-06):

# Front & Rear Differential Assembly

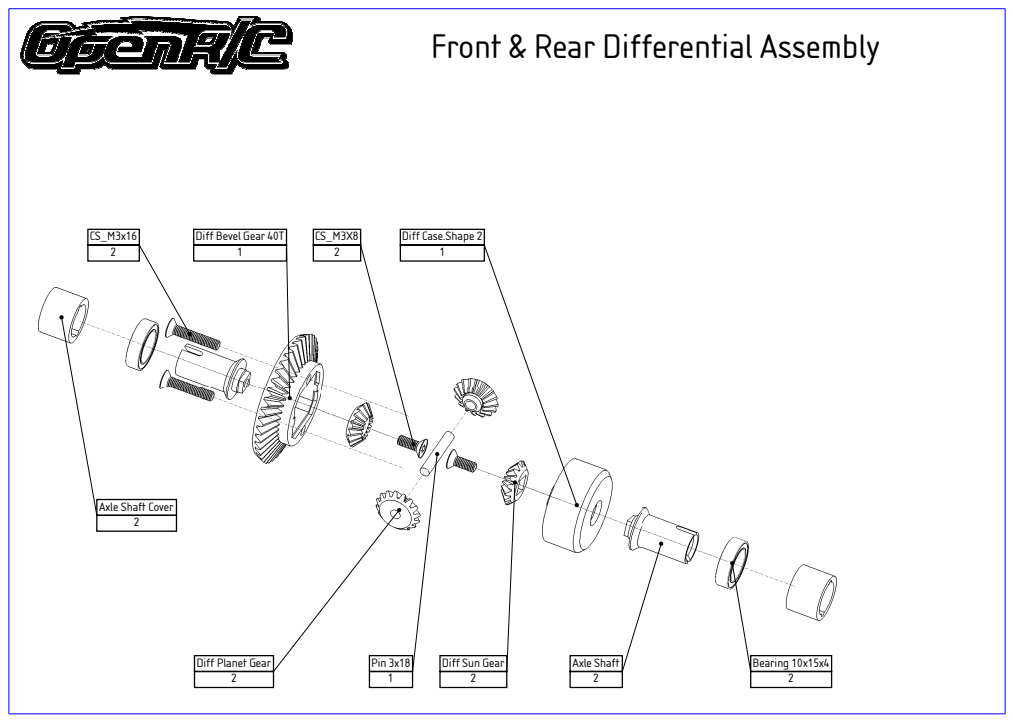
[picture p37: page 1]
Axle Shaft 2; Bearing 10x15x4 2; Pin 3x18 1

Diff Bevel Gear 40T

Diff Case.Shape 2

Axle Shaft Cover

Diff Planet Gear

Diff Sun Gear

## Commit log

2014-01-04 Initial Check in
    [Axle Shaft Cover.stl, Axle Shaft Cover.stp, Axle Shaft.stl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]
2014-01-05 Added Bill of Materials
2014-01-05 Added an alternate rim from thingiverse
    [my_rim_2.skp]
2014-01-05 added link to motor and ESC. added Truggy Specs.
2014-01-05 linked BOM to truggy readme.
2014-01-05 Add the OZ Rally WRC Wheels
    [M-03_OZ-WRC.stl, my_rim_2.skp]
2014-01-05 reorganized components
    [Left Shield.A.5.stl, Right Shield.A.6.stl, Top Deck Front.A.7.stl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]
2014-01-05 added beadlock rim and organized wheels
    [M-03_OZ-WRC.stl, bead-scalllop.stl, bead-toothed.stl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]
2014-01-05 added RC Crawler 4x4 rim
    [llanta_v1.1.CATPart, llanta_v1.1.igs, llanta_v1.1.stl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]
2014-01-06 Added Andrés Ducted Fan Design Library.
2014-01-06 turned the bill of materials into a markdown file and got rid of the redundant, non hardware bits.
2014-01-06 changed BOM link to md file rather than pdf.
2014-01-06 consildated parts sourcing into BOM
2014-01-06 Updated BOM link to indicate that it has sourcing info
2014-01-06 Added Amazon Supply (formerly small parts) sources for screws
2015-05-06 Updated all files to latest bits.
    [Axle Shaft Cover.stl, Axle Shaft Cover.stp, Axle Shaft.stl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]
2015-05-06 fixed links and images.
    [openrc_new_dxf.dxf]
2016-08-18 Update BOM.md
    Correct bearing size from 3x10x40 to 5x10x4.
    Fix: #2
